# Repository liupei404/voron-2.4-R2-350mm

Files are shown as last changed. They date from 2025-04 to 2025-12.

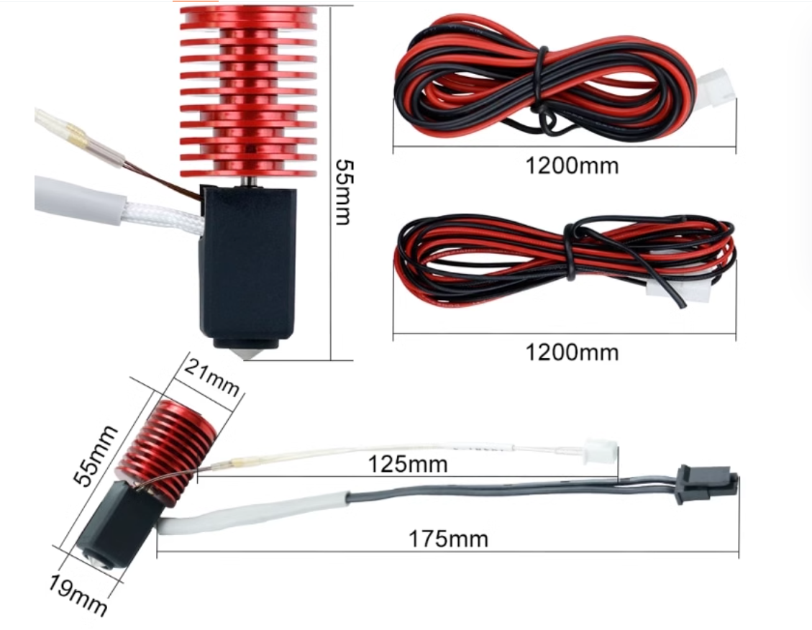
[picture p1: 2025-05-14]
image/V6_hotend2.png

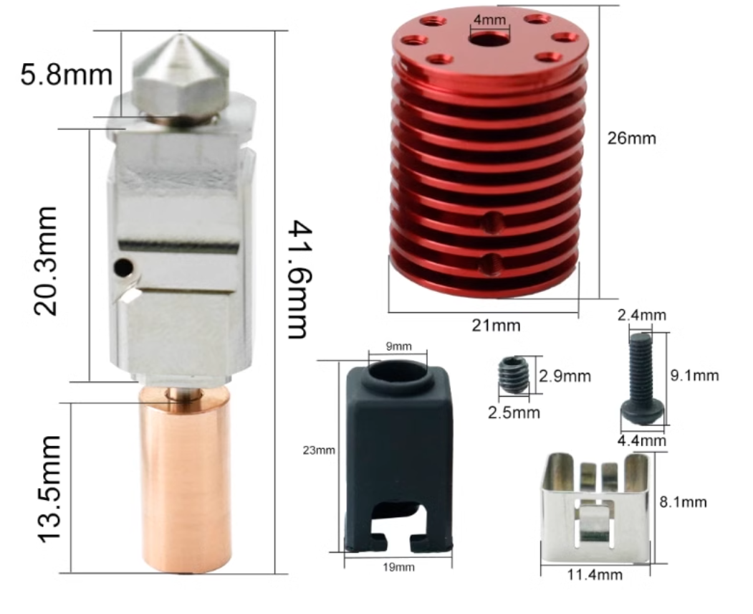
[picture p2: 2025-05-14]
image/V6_hotend1.png

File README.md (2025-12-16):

# voron-2.4-R2-350mm Klipper AMS 之 BoxTurtle龟盒多色系统构建
- 卧龙2.4 R2版本350mm装机，带工具头切刀，BoxTurtle，TN1.0
### 本配置使用如下限位
- 在新版本中原来机械限位不知道怎么设置报错,不得不改用eddy作为限位器
- eddy Eddy 同时作为自动调平传感器和 Z 轴限位开关,beta Z 轴偏移功能

#  打印机主要组件
## 电器配置
- A/B Z电机：17HS19-2004S1-22B 48mm  
- MCU：带BIGTREETECH TMC2209的BIGTREETECH Manta M8P  
- 电源：350W 24V   
- 核心板: BIGTREETECH CB1  
- 显示器：Mellow高清Fly3D隐藏式接线7寸HDMI触摸屏幕  
- 相机：WLZ-NB13M2413 V22广告机免驱广角120度+1300万像素摄像头模组,65mm*9mm*6.7mm。  
- 自动调平传感器IDM涡流电感TAP：BIGTREETECH Eddy  

## USB 工具头
- 挤出机电机：36BYG1204-A-6QHT  
- 工具头：BIGTREETECH EBB SB 2209 USB (自带共振补偿LIS2DW不需要单独购买),装机小心扩展板螺丝不要短路插排,尽量不要带电拔插,主板和电机需要供地。  
- 热端：新款VORON2.4/0.2散热器V6陶瓷热端挤出头高速打印套件24V60W配件  
- 热端风扇：4010 24V磁悬浮静音  
- 模型冷却风扇：5015 24V离心涡轮  
- 挤出机：Clockwork2(双传感器) 为后期多色提供切刀使用(FilamATrix 工具头切刀改件(VORON))改件,不建议使用远程切刀  
- 传感器：D2F-L、D2F-5L(二选一，去掉加长杆，5.55mm钢珠)  
- SB灯光：Mellow Voron-Stealthburner LED灯珠(GRB 10灯珠)  专用打印文件https://cdn.mellow.klipper.cn/STEP/Stealthburner_LED.step  

## 其他配件
- 打完关机模块断电短路检测： BIGTREETECH Relay （暂时没有使用）  
- XY限位开关：FLY3D打印机配件Voron霍尔效应传感器  
- Z限位开关：Mellow Hartk Sexbolt Z轴限位开关注塑套件适用于Voron2.4三叉戟(也可以使用eddy作为限位器,为了安全我还是喜欢使用物理限位器，如果使用eddy作为限位器应  控制好Z高度不要撞机了。)  
- Z轴光轴：圆轴D切5mm 负公差(精密性)  
- Z轴同步轮皮带:GATES环形带188*4  
- 其他皮带：GATES 2GT高精度低粉尘闭口皮带同步  
- 电源滤波: CW4L2-20A-RG（小壳）[20A端子台导轨式]  
- 电器导轨：C45电气导轨镀彩锌加厚  
- 电器仓风扇: 6020 24V 静音  
- 仓室照明：Mellow 370mm RGB灯条 25灯珠  
- 卡式品字插座：AC-01卡式品字插座 带灯开关保险丝  

## 机械&框架
- 框架：通用voron2.4R2 350mm铝型材 （嘉立创FA）  
- X 直线导轨：HIWIN MG 系列微型直线导轨 - MGN12H  
- Y 型直线导轨:HIWIN MG 系列微型直线导轨 - MGN9H  
- Z 轴直线导轨:HIWIN MG 系列微型直线导轨 - MGN9H  
- 单面3M泡沫胶10mm、厚度1mm&3mm  
- 双面3M VHB  

## 床
- 固态继电器：G3NA-210-D/DC5-24V/10A  
- 加热垫：Keenovo 硅胶交流加热器350x350x220x1000W进口定做VORON2.4 350mm  
- 构建台：Mellow高精度CNC加工超平Voron2.4精铸铝热床板,355x355x8mm  
- PEI：弹簧钢双面PEI喷涂355*355mm+磁贴片  

# BoxTurtle 龟盒多色
- 多色推荐使用龟盒,兔子多色调试繁琐 
- https://github.com/ArmoredTurtle/BoxTurtle
- 龟箱不打印裙子right_rear_skirt.stl,使用下面选配件BTIO扩展裙子。
- 
- AFC选配件：AFC_Bypass直通和AT_Brush毛刷(暂时没用),BTIO扩展板需要。
- https://github.com/ArmoredTurtle/AFC-Accessories 

# 多色校准
- 校准单元 AFC_CALIBRATION
- 校准挤出机与轮毂之间的距离或Bowden长度 UNIT_CALIBRATION UNIT=Turtle_1
- 校准选定单元中每个车道的挤出机到轮毂距离 UNIT_LANE_CALIBRATION UNIT=Turtle_1
- 校准选定单元中特定车道的鲍登长度 UNIT_BOW_CALIBRATION UNIT=Turtle_1
- 该功能对AFC内一个或多个车道的轮毂和鲍登长度进行校准 （自动丝控系统）CALIBRATE_AFC LANE=all Bowden=lane1 DISTANCE=30 TOLERANCE=3
CALIBRATE_AFC BOWDEN=lane1` (Calibrates the Bowden length for 'lane1')
- 该功能调节Bowden管在轮毂与刀头之间的长度。 它获取由“HUB”参数指定的集线器和指定的长度调整 由“长度”参数决定。UNLOAD_LENGTH调整卸载鲍登长度。如果没有指定集线器 如果车道当前加载，它会使用当前车道的枢纽。要把长度重置回配置 值，输入每个长度，重置为配置文件中的值。在 长度会增加或减少鲍登长度 SET_BOWDEN_LENGTH HUB=Turtle_1 LENGTH=+100 UNLOAD_LENGTH=-100
## 多色电气
- 远程挤出机:10齿的36圆饼电机 (四通道单独使用)  
- LED: 带灯板WS2812-RGB  
- 主板风扇：3010 轴流风扇 5v(使用开创围挡,没用使用风扇)  
- 回料电机：N20减速电机 6v/500RPM  
- 传感器：D2HW-C201H(推荐使用)  
- 线材：24AWG线材（0.2平方） 
- 主板：带TMC2209的 AFC-Lite 主板  

## 缓冲器
- TN1.0 & TN2.0(不使用TN2.0)  
- 推荐使用TN1.0   
- 传感器：D2F-L 2个(TN1.0使用,TN2.0使用霍尔)  

## 封箱
- 使用三方封箱

- 透明亚克力圆盘:3mm厚度x220mm x2  
- PETG板:1.5mm厚度x533mmx384mm x1

#  Orcaslicer切片软件配置
- 起始代码
- M104 S0 ; 阻止 OrcaSlicer 单独发送温度等待
  M140 S0 ; 阻止 OrcaSlicer 单独发送温度等待
  PRINT_START EXTRUDER=[first_layer_temperature] BED=[first_layer_bed_temperature] CHAMBER=[chamber_temperature] TOOL={initial_tool}

- 耗材丝更换(乌龟多色)
  T[next_extruder] PURGE_LENGTH=[flush_length]
  ;{ if toolchange_count == 1 }
  ;SET_AFC_TOOLCHANGES TOOLCHANGES=[total_toolchanges]{endif }
  ;FLUSH_START
  ;EXTERNAL_PURGE {flush_length}
  ;FLUSH_END

- 耗材材料-单挤出机多材料打印机的换色参数全部设置0.

#  其他
## 挤出机设置计算
- 新款VORON2.4/0.2散热器V6陶瓷热端挤出头高速打印套件24V60W配件 计算方式如下：
- https://github.com/liupei404/voron-2.4-R2-350mm/blob/main/image/V6_hotend1.png
- https://github.com/liupei404/voron-2.4-R2-350mm/blob/main/image/V6_hotend2.png
- https://github.com/liupei404/voron-2.4-R2-350mm/blob/main/image/example-cw2-voron2.4_0.2_new%20V6_hotend.png

## 封箱装配
- https://github.com/liupei404/voron-2.4-R2-350mm/tree/main/BoxTurtle 原版龟盒封箱顶盖Mod/Snipaste_2025-01-16_08-45-27.jpg
-

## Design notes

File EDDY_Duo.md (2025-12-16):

# 校准安装高度
## 确保 Eddy 的安装位置高于喷嘴 2 至 3 毫米

# 固件编译
- [*] Enable extra low-level configuration options 
- Micro-controller Architecture (Raspberry Pi RP2040/RP235x) ---> 
- Processor model (rp2040) ---> 
- Bootloader offset (No bootloader) ---> 
- Flash chip (GENERIC_03H with CLKDIV 4) ---> 
- Communication Interface (USBSERIAL) --->
## 如果不使用 KATAPULT
- Bootloader offset (No bootloader) ---> 
- Flash chip (GENERIC_03H with CLKDIV 4) --->
## 如果使用 KATAPULT（使用此方式需要先进行 5.4 的操作）
- Bootloader offset (16KiB bootloader) --->
## 如果使用 USB 通信 
- Communication Interface (USBSERIAL) --->
## 如果使用 CAN BUS 通信
- Communication interface (CAN bus) ---> 
- (4) CAN RX gpio number 
- (5) CAN TX gpio number 
- (1000000) CAN bus speed

# 校准
##  驱动电流校准
- 将 Eddy 置于热床上方约 20mm 处，LDC_CALIBRATE_DRIVE_CURRENT 
CHIP=btt_eddy
- 将 Eddy 读数映射到喷嘴高度，PROBE_EDDY_CURRENT_CALIBRATE_AUTO CHIP=btt_eddy
### 如果使用手动校准步骤
- G28 X Y 归零
- 清除高度图 BED_MESH_CLEAR
- G0 X175 Y175 F6000 将喷嘴移动到平台中心(350mm平台)
- 开始手动 Z 轴偏移校准 PROBE_EDDY_CURRENT_CALIBRATE CHIP=btt_eddy
## 床面网格校准
- Home 所有轴
- 调平 Z_TILT_ADJUST 或者 QUAD_GANTRY_LEVEL
- 快速的网格扫描 BED_MESH_CALIBRATE METHOD=scan 
SCAN_MODE=rapid

## 温度补偿校准
- Home 所有轴
- G0 Z5 将 Z 轴调整至床面上方 5 毫米
- 执行 SET_IDLE_TIMEOUT TIMEOUT=36000 将机器的 idle timeout 设置长
一点，避免我们升温过程的时候 timeout
- TEMPERATURE_PROBE_CALIBRATE PROBE=btt_eddy TARGET=56 STEP=4(如果要打印高温材料，把温度设置到66以上，不然打印中途会报错无法连接到eddy)
- Eddy 的温度不再上升
- TEMPERATURE_PROBE_NEXT - 可用于在达到步进增量前强制采样新数据
- TEMPERATURE_PROBE_COMPLETE - 可用于在达到目标前完成校准
- ABORT - 可用于终止校准并忽略结果

# 注意：
## 在调试是往往高度混肴导致调试完了报错,和温度补偿温度设置不够，在打印中途停机

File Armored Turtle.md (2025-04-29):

## 热端值

# 设置热端特定值
AFC 的一些值非常依赖于您的热端

热端类型的建议起始值（更多内容将在后面添加）如下。 和 在 中，并且 在 中。对于 ，如果已定义，请使用第二个值;否则，请使用 第一个值。
如果您使用 ram 缓冲区作为工具头传感器，则可能需要增加此值。
tool_stntool_stn_unloadAFC/AFC_Hardware.cfgvariable_retract_lengthvariable_pushback_lengthAFC/AFC_Macro_Vars.cfgtool_stnpin_tool_end

以下是 FilamATrix/Clockwork 2 上的 Voron2.4/ 0.2 新款V6 热端的示例图：

## 热端特定值

新款V6 
tool_stn： 59 （如果未定义） / 36 （如果已定义）pin_tool_endpin_tool_end
tool_stn_unload: 106
variable_retract_length: 26.1
variable_pushback_length: 20

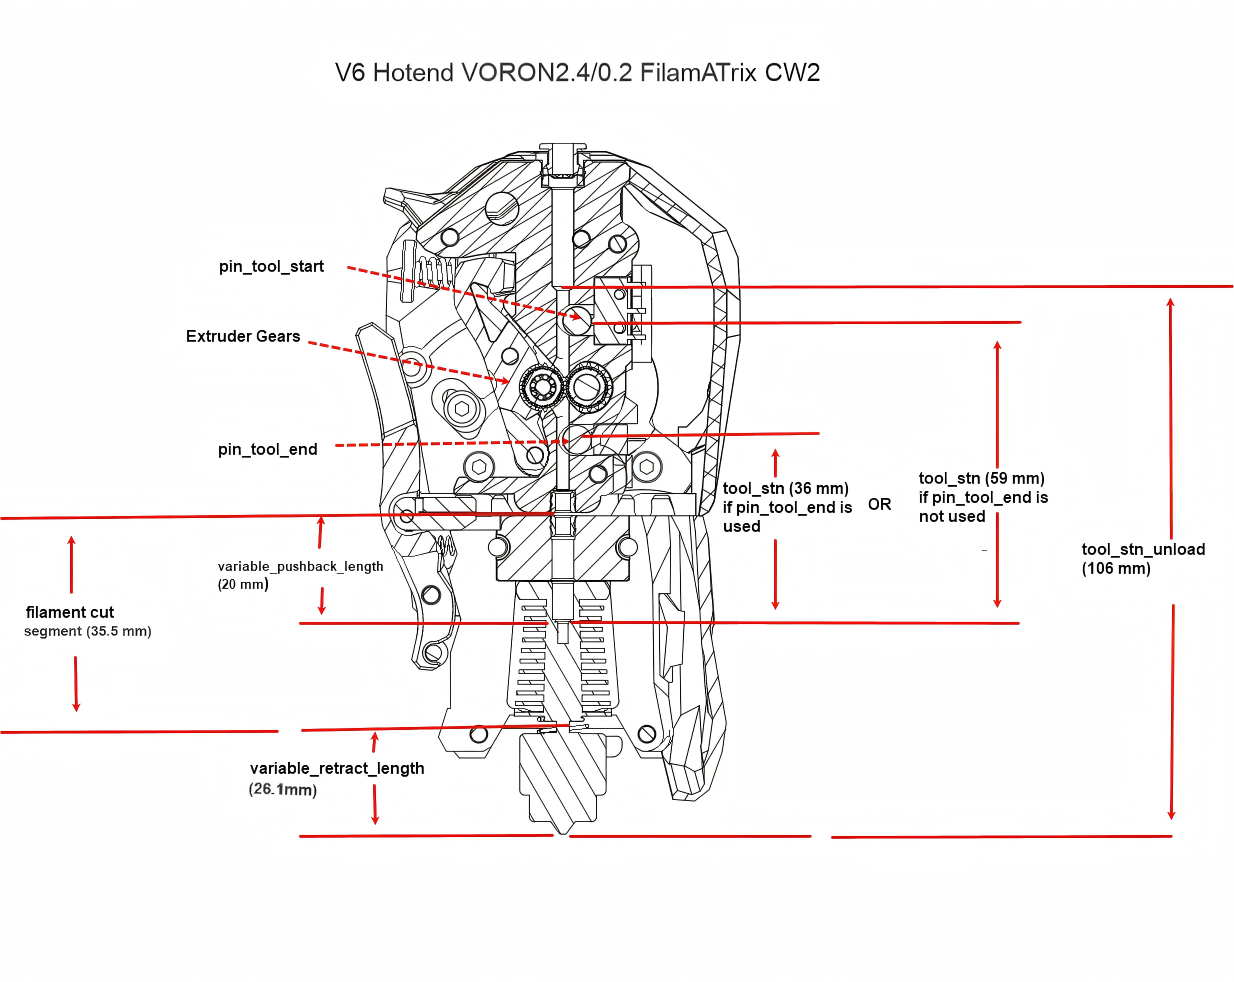
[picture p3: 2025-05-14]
image/example-cw2-voron2.4_0.2_new V6_hotend.png

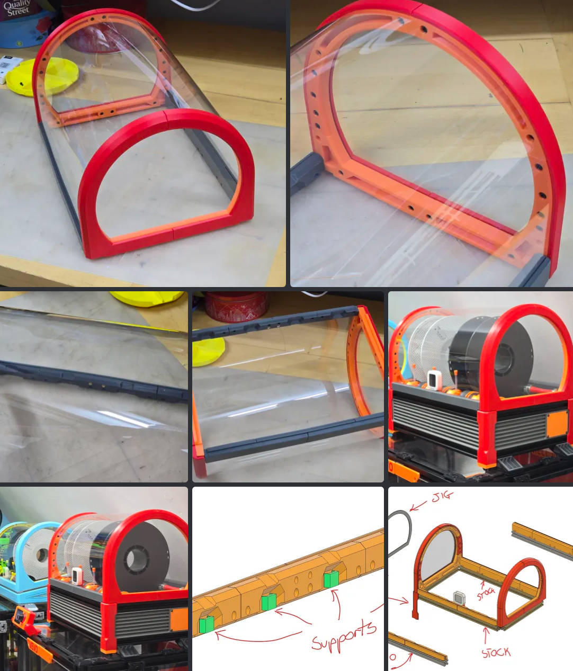
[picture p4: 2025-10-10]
BoxTurtle 原版龟盒封箱顶盖Mod/Snipaste_2025-01-16_08-45-27.jpg

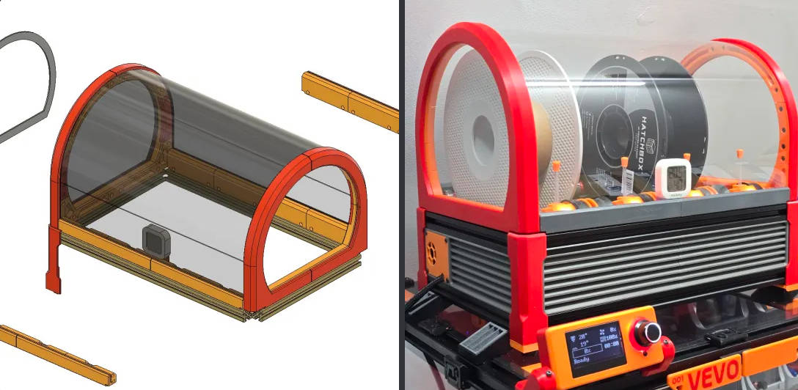
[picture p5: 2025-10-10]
BoxTurtle 原版龟盒封箱顶盖Mod/Snipaste_2025-01-16_08-45-38.jpg

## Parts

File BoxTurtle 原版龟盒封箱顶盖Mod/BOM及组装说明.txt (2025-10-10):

https://docs.qq.com/sheet/DQnRyZGNRQk15SGt2?tab=xqy0mo

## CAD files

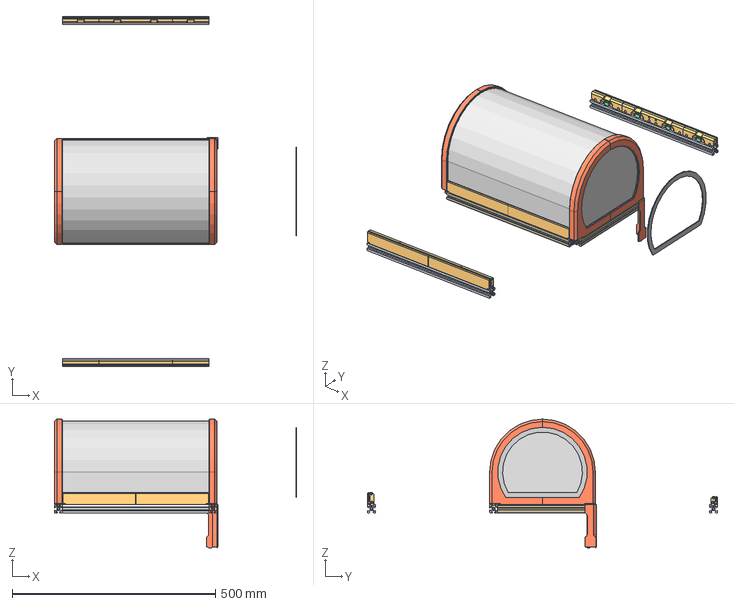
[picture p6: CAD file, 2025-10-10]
BoxTurtle 原版龟盒封箱顶盖Mod/BT 3D Printed Top Hat Stock v1_1.step
595.5 x 860.0 x 316.4 mm

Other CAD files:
BoxTurtle 原版龟盒封箱顶盖Mod/BT 3D Printed Top Hat Stock v1_1___15_01_25.f3d

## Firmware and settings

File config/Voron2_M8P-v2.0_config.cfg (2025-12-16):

# This file contains common pin mappings for the BIGTREETECH Manta M8P V2.0
# To use this config, the firmware should be compiled for the
# STM32H723 with a "8KiB bootloader" and USB communication.

# This config is currently only correct for V2.0 boards
# 
# See docs/Config_Reference.md for a description of parameters.

[mcu]
##	[X in MOTOR1] - B Motor
##	[Y in MOTOR2] - A Motor
##	[E in MOTOR8] - Extruder
##	Obtain definition by "ls /dev/serial/by-id/*" then unplug to verify
##--------------------------------------------------------------------
serial: /dev/serial/by-id/usb-Klipper_stm32h723xx_37000B000551323235363233-if00
#restart_method: command
##--------------------------------------------------------------------

[printer]
kinematics: corexy          # 运动学结构，Voron 2.4是corexy
max_velocity: 500           # XY轴最大运动速度
max_accel: 3000    			# XY轴最大运动加速度，Max 4000
max_z_velocity: 5 			# Z轴最大运动速度，Max 15 for 12V TMC Drivers, can increase for 24V 
max_z_accel: 500            # Z轴最大运动加速度
square_corner_velocity: 5.0 # 直角拐弯速度，默认5，小一点可以有效避免惯性造成打印机晃动

[temperature_sensor chamber]
sensor_type:Generic 3950
sensor_pin: PC5
#min_temp:
#max_temp:
#   See the "extruder" section for the definition of the above
#   parameters.
#gcode_id:
#   See the "heater_generic" section for the definition of this
#   parameter.

[temperature_sensor MCU]
sensor_type: temperature_mcu

[temperature_sensor SoC]
sensor_type: temperature_host

#####################################################################
# 	.X/Y 步进设置
#####################################################################

## X Stepper on Motor1(B Motor)
[stepper_x]
step_pin: PE6
dir_pin: !PE5
enable_pin: !PC14
microsteps: 16
rotation_distance: 40
full_steps_per_rotation:200  #set to 400 for 0.9 degree stepper
endstop_pin: ^PF4
position_min: 0
##--------------------------------------------------------------------

##	Uncomment below for 250mm build
#position_endstop: 250
#position_max: 250

##	Uncomment for 300mm build
#position_endstop: 300
#position_max: 300

##	Uncomment for 350mm build
position_endstop: 350
position_max: 350

##--------------------------------------------------------------------
homing_speed: 25   #Max 100
homing_retract_dist: 5
homing_positive_dir: true

##	Make sure to update below for your relevant driver (2208 or 2209)
[tmc2209 stepper_x]
uart_pin: PC13
interpolate: True
run_current: 0.8
sense_resistor: 0.110
stealthchop_threshold: 0

## Y Stepper on Motor2 (A Motor)
[stepper_y]
step_pin: PE2
dir_pin: !PE1
enable_pin: !PE4
microsteps: 16
rotation_distance: 40
endstop_pin: ^PF3
full_steps_per_rotation:200  #set to 400 for 0.9 degree stepper
position_min: 0
##--------------------------------------------------------------------

##	Uncomment for 250mm build
#position_endstop: 250
#position_max: 250

##	Uncomment for 300mm build
#position_endstop: 300
#position_max: 300

##	Uncomment for 350mm build
position_endstop: 340
position_max: 340

##--------------------------------------------------------------------
homing_speed: 25  #Max 100
homing_retract_dist: 5
homing_positive_dir: true

##	Make sure to update below for your relevant driver (2208 or 2209)
[tmc2209 stepper_y]
uart_pin: PE3
interpolate: True
run_current: 0.8
sense_resistor: 0.110
stealthchop_threshold: 0

#####################################################################
# 	Z Stepper Settings
#####################################################################

## Z0 Stepper - Front Left on MOTOR3_A
[stepper_z]
step_pin: PB8
dir_pin: !PB7
enable_pin: !PE0
rotation_distance: 40
gear_ratio: 80:16
microsteps: 16
# endstop_pin: ^PF2
endstop_pin: probe:z_virtual_endstop
##  Z-position of nozzle (in mm) to z-endstop trigger point relative to print surface (Z0)
##  (+) value = endstop above Z0, (-) value = endstop below
##	Increasing position_endstop brings nozzle closer to the bed
##  After you run Z_ENDSTOP_CALIBRATE, position_endstop will be stored at the very end of your config
#position_endstop: -0.475 #限位开关的位置（以毫米为单位）
# position_endstop: 0.525 #限位开关的位置（以毫米为单位）
##--------------------------------------------------------------------

##	Uncomment below for 250mm build
#position_max: 240

##	Uncomment below for 300mm build
#position_max: 290

##	Uncomment below for 350mm build
position_max: 310 #最大有效距离

##--------------------------------------------------------------------
position_min: -5 # 用户可以命令步进器移动到的最小有效距离（以毫米为单位）
homing_speed: 8 #步进器在归位时的最大速度（以毫米/秒为单位）
second_homing_speed: 3 #在进行第二次归位时步进器的速度（以毫米/秒为单位）。默认值是homing_speed的一半
homing_retract_dist: 3 #在归位过程中第二次归位之前的后退距离（以毫米为单位）

##	Make sure to update below for your relevant driver (2208 or 2209)
[tmc2209 stepper_z]
uart_pin: PB9
interpolate: true
#   如果为真，则启用步进插值（驱动器将以256微步的速度内部步进）。
#   只有当microsteps设置为16时，这才有效。插值会引入了极小的系统性位置
#   偏差 - 有关详细信息，请参见TMC_Drivers.md。
#   默认为True
run_current: 0.8
#   配置驱动器在步进电机移动期间使用的电流（以安培RMS为单位）。
#   必须提供此参数
sense_resistor: 0.110
stealthchop_threshold: 50
#   设定“StealthChop”阈值的速度（以毫米/秒为单位）。当设定时，如果步进
#   电机的速度低于此值，“StealthChop”模式将被启用。
#   默认值为0，此值会禁用“StealthChop”模式

##	Z1 Stepper - Rear Left on Motor5
[stepper_z1]
step_pin: PG13
dir_pin: PG12    #电机方向引脚设置
enable_pin: !PG15
rotation_distance: 40    #同步轮周长mm
gear_ratio: 80:16
microsteps: 16    #细分

##	Make sure to update below for your relevant driver (2208 or 2209)
[tmc2209 stepper_z1]
uart_pin: PG14
interpolate: true
run_current: 0.8
sense_resistor: 0.110
stealthchop_threshold: 50

##	Z2 Stepper - Rear Right on Motor6
[stepper_z2]
step_pin: PG9
dir_pin: !PD7
enable_pin: !PG11
rotation_distance: 40
gear_ratio: 80:16
microsteps: 16

##	Make sure to update below for your relevant driver (2208 or 2209)
[tmc2209 stepper_z2]
uart_pin: PG10
interpolate: true
run_current: 0.8
sense_resistor: 0.110
stealthchop_threshold: 50

##	Z3 Stepper - Front Right on Motor7
[stepper_z3]
step_pin: PD4
dir_pin: PD3
enable_pin: !PD6
rotation_distance: 40
gear_ratio: 80:16
microsteps: 16

##	Make sure to update below for your relevant driver (2208 or 2209)
[tmc2209 stepper_z3]
uart_pin: PD5
interpolate: true
run_current: 0.8
sense_resistor: 0.110
stealthchop_threshold: 50

#####################################################################
# 	Extruder
#####################################################################

#	E0 on Motor8
# [extruder]
# step_pin: PC7
# dir_pin: PC8
# enable_pin: !PD2
##  Update value below when you perform extruder calibration
##  If you ask for 100mm of filament, but in reality it is 98mm:
##  rotation_distance = <previous_rotation_distance> * <actual_extrude_distance> / 100
##  22.6789511 is a good starting point
# rotation_distance: 22.6789511   #Bondtech 5mm Drive Gears
##  Update Gear Ratio depending on your Extruder Type
##  Use 50:10 for Stealthburner/Clockwork 2
##  Use 50:17 for Afterburner/Clockwork (BMG Gear Ratio)
##  Use 80:20 for M4, M3.1
# gear_ratio: 50:10
# microsteps: 16
# full_steps_per_rotation: 200	#200 for 1.8 degree, 400 for 0.9 degree
# nozzle_diameter: 0.400
# filament_diameter: 1.75
# heater_pin: PA0
##	Validate the following thermistor type to make sure it is correct

## Check what thermistor type you have. See https://www.klipper3d.org/Config_Reference.html#common-thermistors for common thermistor types.
## Use "Generic 3950" for NTC 100k 3950 thermistors
# sensor_type:Generic 3950

# sensor_pin: PB0
# min_temp: 10
# max_temp: 270
# max_power: 1.0
# min_extrude_temp: 170
# control = pid
# pid_kp = 26.213
# pid_ki = 1.304
# pid_kd = 131.721
##	Try to keep pressure_advance below 1.0
#pressure_advance: 0.05
##	Default is 0.040, leave stock
#pressure_advance_smooth_time: 0.040

##	E0 on Motor7
##	Make sure to update below for your relevant driver (2208 or 2209)
# [tmc2209 extruder]
# uart_pin: PC6
# interpolate: false
# run_current: 0.5
# sense_resistor: 0.110
# stealthchop_threshold: 0

#[filament_switch_sensor material_0]
#switch_pin: PC1

#[filament_switch_sensor material_1]
#switch_pin: PC2

#####################################################################
# 	Bed Heater
#####################################################################

[heater_bed]
##	SSR Pin - HE1
heater_pin: PA1
## Check what thermistor type you have. See https://www.klipper3d.org/Config_Reference.html#common-thermistors for common thermistor types.
## Use "Generic 3950" for NTC 100k 3950 thermistors
sensor_type:Generic 3950
sensor_pin: PB1
##  Adjust max_power so it doesn't exceed the SSR rating. The Omron G3NA-210B-DC5 SSR is rated at 4 amps without a heatsink.
##  The formula is "4 / (Wattage_of_bed_heater / Mains_voltage) = max_power"
##  If max_power is greater than 1.0, use 1.0
max_power: 1.0
min_temp: 0
max_temp: 130
## 校准 PID 设置 PID_CALIBRATE HEATER=heater_bed TARGET=100
control: pid
pid_kp: 55.629
pid_ki: 2.303
pid_kd: 335.860

#####################################################################
# 	Probe
#####################################################################
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

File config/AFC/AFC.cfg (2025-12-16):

[AFC]
VarFile: /home/biqu/printer_data/config/AFC/AFC.var   # Path to the variables file for AFC configuration.

#--=================================================================================-
#------- Speed ----------------------------------------------------------------------
#--=================================================================================-
long_moves_speed: 150           # mm/s. Default value is 150mm/s.
long_moves_accel: 250           # mm/s². Default value is 250mm/s².
short_moves_speed: 50           # mm/s. Default value is 50mm/s.
short_moves_accel: 300          # mm/s². Default value is 300mm/s².
short_move_dis: 10              # Move distance for failsafe moves. Default is 10mm.

#global_print_current: 0.6       # Uncomment to set stepper motors to a lower current while printing
                                # This value can also be set per stepper with print_current: 0.6
enable_sensors_in_gui: True     # Uncomment to show all sensor switches as filament sensors in mainsail/fluidd gui
                                # this can also be set at individual levels in your config file
default_material_temps: default: 235, PLA:210, PETG:235, ABS:235, ASA:235 # Default temperature to set extruder when loading/unloading lanes.
                                                  # Material needs to be either manually set or uses material from spoolman if extruder temp is not
                                                  # set in spoolman. Follow current format to add more
common_density_values: PLA:1.24, PETG:1.23, ABS:1.04, ASA:1.07 # Generic default density values.  Follow current format to add more
#default_material_type: PLA      # Default material type to assign to a spool once loaded into a lane

load_to_hub: True               # Fast loads filament to hub when inserted, set to False to disable. This is a global setting and can be overridden at AFC_stepper
#moonraker_port: 7125            # Port to connect to when interacting with moonraker. Used when there are multiple moonraker/klipper instances on a single host

assisted_unload: True           # If True, the unload retract is assisted to prevent loose windings, especially on full spools. This can prevent loops from slipping off the spool. This is a global setting and can be overridden at the unit and stepper level.
#pause_when_bypass_active: True  # When True AFC pauses print when change tool is called and bypass is loaded
#unload_on_runout: True          # When True AFC will unload lane and then pause when runout is triggered and spool to swap to is not set(infinite spool)
#print_short_stats: True          # Set to true to print AFC_STATS in short form instead of wide form, printing short form is better for consoles that are small in width
#debug: True                     # Setting to True turns on more debugging to show on console

#--=================================================================================-
#------- TRSYNC Values --------------------------------------------------------------
#--=================================================================================-
#trsync_update: True           # Uncomment this value to update Klipper's trsync value automatically
#trsync_timeout: 0.05          # Uncomment this value if timeout needs to be greater than the default of 0.05
#trsync_single_timeout: 0.250  # Uncomment this value if single_timeout needs to be greater than the default of 0.250

#--=================================================================================-
#------- Pause/Resume ---------------------------------------------------------------
#--=================================================================================-
z_hop: 5                        # Height to move up before and after a tool change completes
resume_speed: 120               # Speed mm/s of resume move. Set to 0 to use gcode speed
resume_z_speed: 30              # Speed mm/s of resume move in Z. Set to 0 to use gcode speed
error_timeout: 36000            # Time in seconds to pause when an error is detected.
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

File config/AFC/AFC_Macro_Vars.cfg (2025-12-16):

[include macros/*.cfg]

#--=================================================================================-
#------- Global ---------------------------------------------------------------------
#--=================================================================================-
[gcode_macro _AFC_GLOBAL_VARS]
description: Global variables used in multiple macros
gcode: # Leave Empty

# Set this to match your AFC_stepper base naming in AFC_Hardware.cfg
variable_stepper_name             : 'lane'    # [AFC_stepper lane1] [AFC_stepper lane2]...

variable_travel_speed             : 120       # Speed mm/s
variable_z_travel_speed           : 30        # Speed mm/s
variable_accel                    : 2000      # Move accel for all macro moves
variable_disable_skew_correction  : False      # When True macros will disable and re-enable skew correction while performing kinematic actions, useful if you took your measurements before loading your skew profiles which may limit where the toolhead can go during print.
variable_verbose                  : 1         # Console Output for macros
                                              #  0 - None
                                              #  1 - Limited
                                              #  2 - All


#--=================================================================================-
#------- Cut -----------------------------------------------------------------------
#--=================================================================================-
[gcode_macro _AFC_CUT_TIP_VARS]
description: Toolhead tip cutting macro configuration variables
gcode: # Leave empty

# This should be the position of the toolhead where the cutter arm just
# lightly touches the depressor pin
variable_pin_loc_xy               : 8, 50.39    # x,y coordinates of depressor pin

# Accel during cut. This will overwrite the global accel for this macro. Set to 0 to use global accel
variable_cut_accel                : 0

# Direction to make the cut move (left, right, front, back)
variable_cut_direction            : "left"

# This distance is used to move toolhead to cut filament
# and to create a small safety distance that aids in generating momentum
variable_pin_park_dist            : 6.0       # Distance in mm

# Position of the toolhead when the cutter is fully compressed.
# Distance the toolhead needs to travel to compress the cutter arm.
# To calculate this distance start at the pin_loc_xy position and move
# your toolhead till the cutter arm is completely compressed. Take 0.5mm off this distance
# as a buffer. 
# Ex pin_loc_x : 9, 310  fully compressed at 0, 310 set cut_move_dist to 8.5
variable_cut_move_dist            : 8.0       # Distance in mm

# Speed related settings for tip cutting
# Note that if the cut speed is too fast, the steppers can lose steps.
# Therefore, for a cut:
# - We first make a fast move to accumulate some momentum and get the cut
#   blade to the initial contact with the filament
# - We then make a slow move for the actual cut to happen 
variable_cut_fast_move_speed      : 32        # Speed mm/s
variable_cut_slow_move_speed      : 10        # Speed mm/s
variable_evacuate_speed           : 150       # Speed mm/s
variable_cut_dwell_time           : 50        # Time to dwell at the cut point in ms
variable_cut_fast_move_fraction   : 0.85      # Fraction of the move that uses fast move 0.0 - 1.0
variable_extruder_move_speed      : 25        # Speed mm/s for all extruder movement

# If the toolhead returns to initial position after the cut is complete.
variable_restore_position         : False     # True = return to initial position, False = don't return

# Distance to retract prior to making the cut, this reduces wasted filament but might cause clog 
# if set too large and/or if there are gaps in the hotend assembly 
# *This must be less than the distance from the nozzle to the cutter
variable_retract_length           : 26

# This can help prevent clogging of some toolheads by doing a quick tip from to reduce stringing
variable_quick_tip_forming        : False

# Number of times to run the cut movement
variable_cut_count                : 2

# Retract length and speed after the cut so that the cutter can go back 
# into its origin position
variable_rip_length               : 1.0       # Distance in mm to retract to aid lever decompression (>= 0)
variable_rip_speed                : 3         # Speed mm/s

# Pushback of the remaining tip from the cold end into the hotend
# *Must be less then retract_length
variable_pushback_length          : 20        # Distance in mm
variable_pushback_dwell_time      : 20        # Time to dwell between the pushback

# Safety margin for fast vs slow travel. When traveling to the pin location
# we make a safer but longer move if we are closer to the pin than this
# specified margin. Usually setting these to the size of the toolhead
# (plus a small margin) should be good enough 
variable_safe_margin_xy           : 30, 30    # Approx toolhead width +5mm, height +5mm)

# Some printers may need a boost of power to complete the cut without skipping steps.
# One option is to increase the current for the steppers in printer.cfg. Another
# option is to use these variables to set a current that is only used during the
# cut motion. Different combinations of kinematics and cutter configurations engage
# different combinations of steppers for that motion.  Set the needed variables.
# The override is skipped if the current is 0.

# Enable if layer shifts occur when cutting
# variable_cut_current_stepper_x: 0
# variable_cut_current_dual_carriage: 0  # This is the value that is used to define the current for the dual carriage stepper (2nd x) for an IDEX printer during the cut.
# variable_cut_current_stepper_y: 0
# variable_cut_current_stepper_z: 0

# Change these to match the entries in printer.cfg if needed
# variable_conf_name_stepper_x: "tmc2209 stepper_x"
# variable_conf_name_dual_carriage: "tmc2209 dual_carriage"
# variable_conf_name_stepper_y: "tmc2209 stepper_y"
# variable_conf_name_stepper_z: "tmc2209 stepper_z"
# variable_awd: True

# Addon variables for cutter pin servo control
#variable_tool_servo_enable        : False
#variable_tool_servo_name          : "tool_cut"
#variable_tool_servo_angle_out     : 115
#variable_tool_servo_angle_in      : 0

#--=================================================================================-
#------- Poop ----------------------------------------------------------------------
#--=================================================================================-
[gcode_macro _AFC_POOP_VARS]
description: Poop macro configuration variables
gcode: # Leave empty


variable_purge_loc_xy             : 10, 336    # (x,y) Location of where to purge
variable_purge_spd                : 6.5       # Speed, in mm/s, of the purge.
variable_z_purge_move             : True      # Set to False to not move in Z during poop

# Speed, in mm/s to lift z after the purge is completed. Its a faster lift to keep it from 
# sticking to the toolhead
variable_fast_z                   : 200
variable_z_lift                   : 10        # Z height to raise above the final purge position after the purge is completed as part of the fast z move
                                              # example: If final poop height ends at 20mm this variable will raise Z to 30mm

# If the toolhead returns to initial position after the poop is complete.
variable_restore_position         : False     # True = return to initial position, False = don't return

# The z height of the nozzle at the purge position before purging. This allows any built up
# pressure to escape before the purge.

variable_purge_start              : 0.6

# Set the part cooling fan speed. Disabling can help prevent the nozzle from cooling down 
# and stimulate flow, Enabling it can prevent blobs from sticking together.
variable_part_cooling_fan         : True      # Run it at full speed
variable_part_cooling_fan_speed   : 1.0       # Speed to run fan when enabled above. 0 - 1.0
variable_purge_cool_time          : 2         # Time to pause after purge to allow fan to cool the poop in seconds

# ==================== PURGE LENGTH TUNING
# Default purge length to fall back on when neither the tool map purge_volumes or 
# parameter PURGE_LENGTH is set.
variable_purge_length             : 72.111

# The absolute minimum to purge, even if you don't changed tools. This is to prime the 
# nozzle before printing
variable_purge_length_minimum     : 60.999

# The slicer values often are a bit too wasteful. Tune it here to get optimal values. 0.6
# is a good starting point.
#variable_purge_length_modifier    : 1
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

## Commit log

2025-05-14 更新配置
    配置更新
    [AFC.cfg, AFC_Hardware.cfg, AFC_Lite.cfg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]
2025-06-04 预设
    预设
2025-09-21 更新配置文件
    [AFC_Hardware.cfg, AFC_Macro_Vars.cfg, AFC_Turtle_1.cfg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]
2025-09-27 更新打印机预设集，材料预设集
    更新打印机预设集，材料预设集
2025-10-10 修改自述文件，增加三方龟箱封箱文件，修改预设包
    修改自述文件，增加三方龟箱封箱文件，修改预设包
    [BT 3D Printed Top Hat Stock v1_1.step, BT 3D Printed Top Hat Stock v1_1___15_01_25.f3d]
2025-12-16 更新配置使用eddy限位和偏移
    更新配置使用eddy限位和偏移
    [AFC.cfg, AFC_Hardware.cfg, AFC_Lite.cfg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]
